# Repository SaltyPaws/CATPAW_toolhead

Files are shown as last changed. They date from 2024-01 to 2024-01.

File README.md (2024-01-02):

# CATPAW_toolhead

CatPaw is the ideal toolhead for Voron Zero series with Orbiter 2.0 Extruder. I developed this toolhead as I was unhappy with the existing options. The standard Voron Zero 0.2 toolhead does not provide as much cooling as I prefer, and certainly less than the StealthBurner toolhead. My design goals were also minimum loss of print volume and maximum compatibility with toolheads and options for probe and filament sensor.

CATPAW:
- Uses Voron Zero 0.2 toolhead cartridges, so should work with all toolheads for voron Zero 0.2 (fan saver recommended)
- 2x 4010 Blowers, with StealthBurner duct layout for near arctic level part cooling (2x 4010 provides more air than StealthBurner toolhead)
- Almost no loss in print volume. X axis should be full width, loss off a millimeter or so on X if you print with your door closed. (Magnets on my door are strong enough, so the door closes again if the toolhead bumps into it, giving me the full 120x120 mm even when printing ABS
- Option to add the slideswipe Probe. I shortened the probe, but all other parts can be used from https://github.com/SaltyPaws/Voron_0.1and0.2mods/SlideSwipe or original repo (https://github.com/chestwood96/SlideSwipe)
- Option to add under extruder filament Sensor
- Carriages are provided for MGN7 and MGN9 X-axis rails. It is recommended to print the provided X carriage for the appropriate rail. In order to minimize toolhead height, I lowered the screw hole for the rear mounting screw.
The CATPAW toolhead will work with the stock Voron Zero 0.2 Carriage, but the screw securing the X-carriage from the rear will not fit.

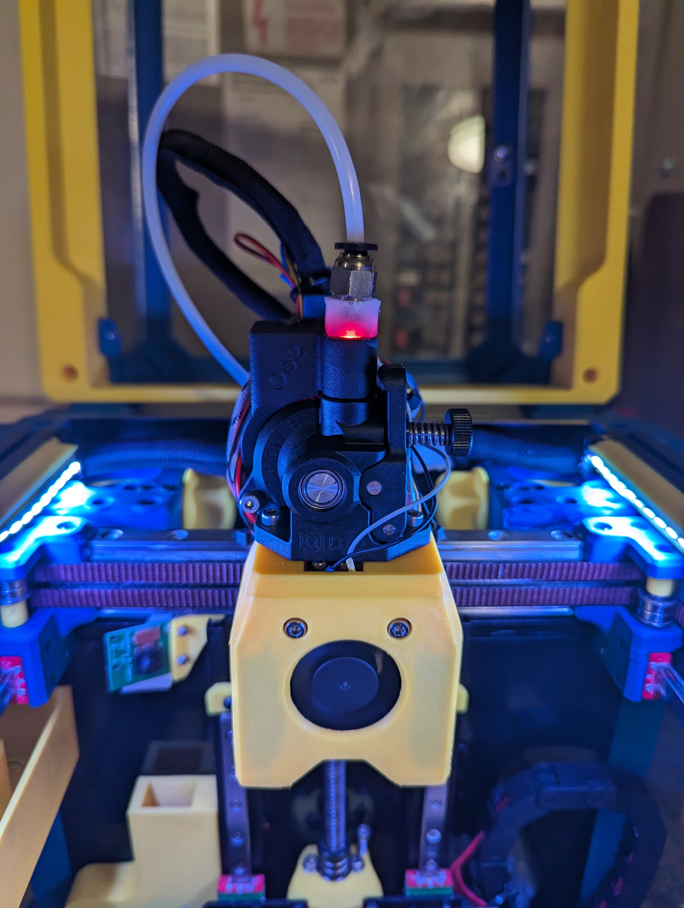
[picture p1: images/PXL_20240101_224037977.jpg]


**BOM**
1. 2x SHCS (preferred) or BHSC M3x25 bolt
2. 3x M3 nut
3. 2x NeoPixel
4. 1x 3010 hotend fan
5. 2x 4010 Blower
6. 6x3mm magnets for probe (optional)
7. 6mm steel ball for filament sensor (optional)
8. Omron D2F-L micro-switch with lever for filament sensor (optional)
9. 2x M2x12 or self-tapping screw to secure micro-switch (optional)

# Installation Instructions
Assembly should be done in the following order:
**Probe**
- Solder wires to 6x3mm magnets. In order to prevent loss of magnetism, let the magnets cool against another 6x3 magnet.
- Press the magnets into the slots by pushing the toolhead down on a hard object.
- Use a large flat soldering tip at around 230C to push the magnets deeper into the slots, you want the magnets to stick out ~0.5 to 1 mm. Again, let the magnets cool down attached to other magnets to prevent loss of magnetism.
- Ensure wire to magnet path has very low resistance (less than 4 ohm).
- route wires out trough little side window.
- Seal hole with red gasket maker.

**NeoPixels**
- Create a chain of 2 neopixels. You do not have a lot of space to hide excess cable, so make the wires between the neopixels as short as possible, while still allowing them to slide into the slots.
- Test the neopixels! It will be more rework to remove the hotend fan and part cooling fans later.

**Fans**
- First install 3010 part cooling fan. Be very careful to only press the edges of the fan, the fan will break when pushing the center of the fan (ask me how I know...)
- Then proceed with installing the blower fans.
- Use a knife to cut the upper right hand side of the blower fan (looking back to front). This is required for routing the majority of the wires. I used superglue to keep the fan together as you will remove a fan closing latch. I accidentally cut int the fan-box, and sealed up the hole with red gasket maker. For details - see pictures below:

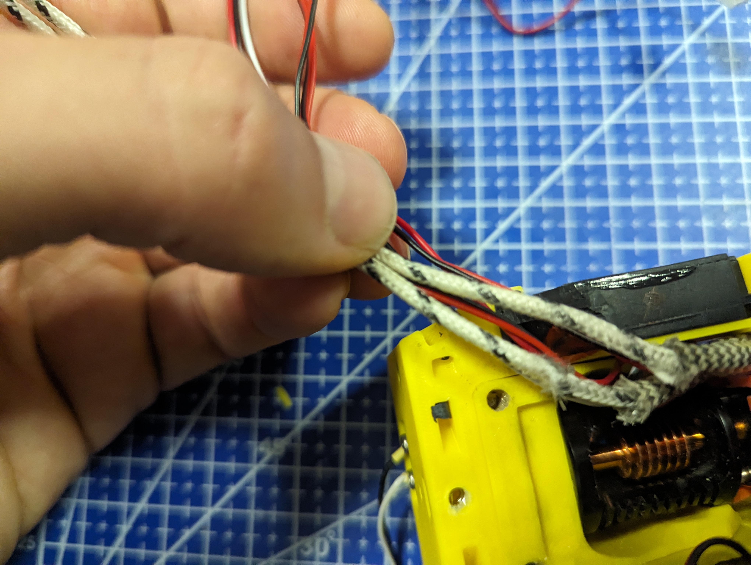
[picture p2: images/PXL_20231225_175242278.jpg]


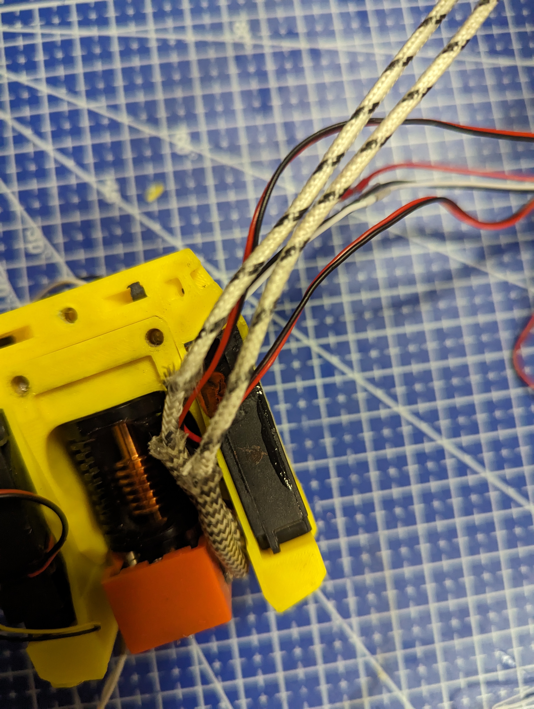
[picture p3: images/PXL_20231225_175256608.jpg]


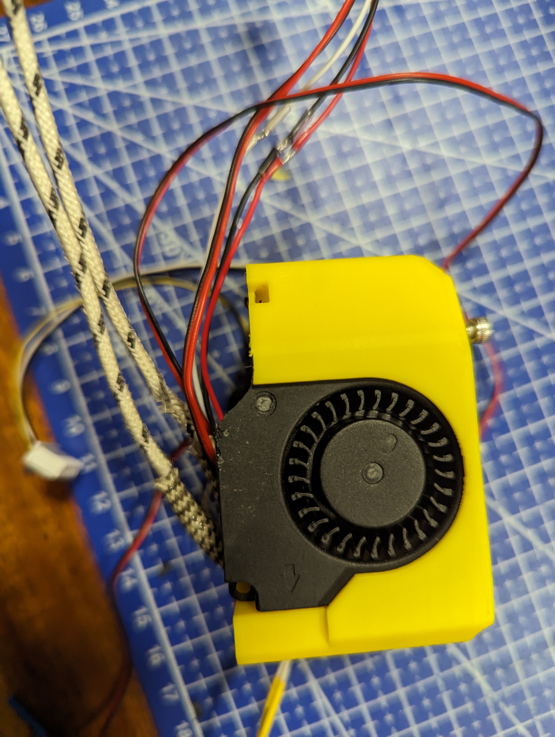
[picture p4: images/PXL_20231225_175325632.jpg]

  
**Toolhead Cartridge**
- Ensure the heater wires are installed pointing towards the right hand fan that has space for wire routing.
- Thermistor, probe and fan wires will fit on the other side (left hand side fan).
- Hold off on installing the zip-ties, these are best installed after the toolhead is installed on the carriage.

**Filament Sensor**  
- Solder wires to filament sensor (2 outermost legs). You may want to shorten the legs somewhat for an easier fit.
- Trim lever, so that lever does not extend past micro-switch body
- Install micro-switch and ball
- Test sensor

**Install Toolhead**
- Carefully mount toolhead, ensuring that wires are not pinched, and belt is not rubbing on gantry. The bulk of the wires will go in the gap carved out on the right hand side fan, the other side will have sufficient space for probe and fan wires.
- 
**Min Probe**
- See installation instructions in orignal repo: https://github.com/chestwood96/SlideSwipe

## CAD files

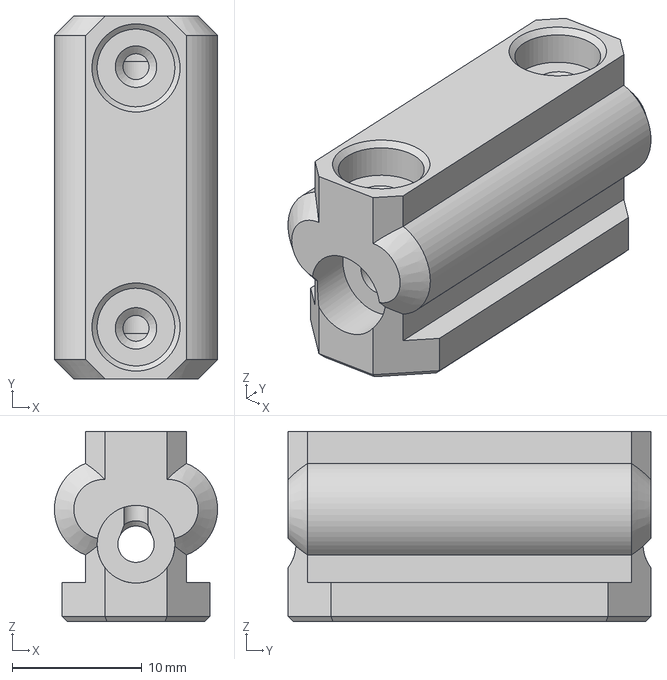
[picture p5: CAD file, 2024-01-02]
CAD/Mini_ProbeTight v3.step
12.6 x 28.0 x 14.7 mm

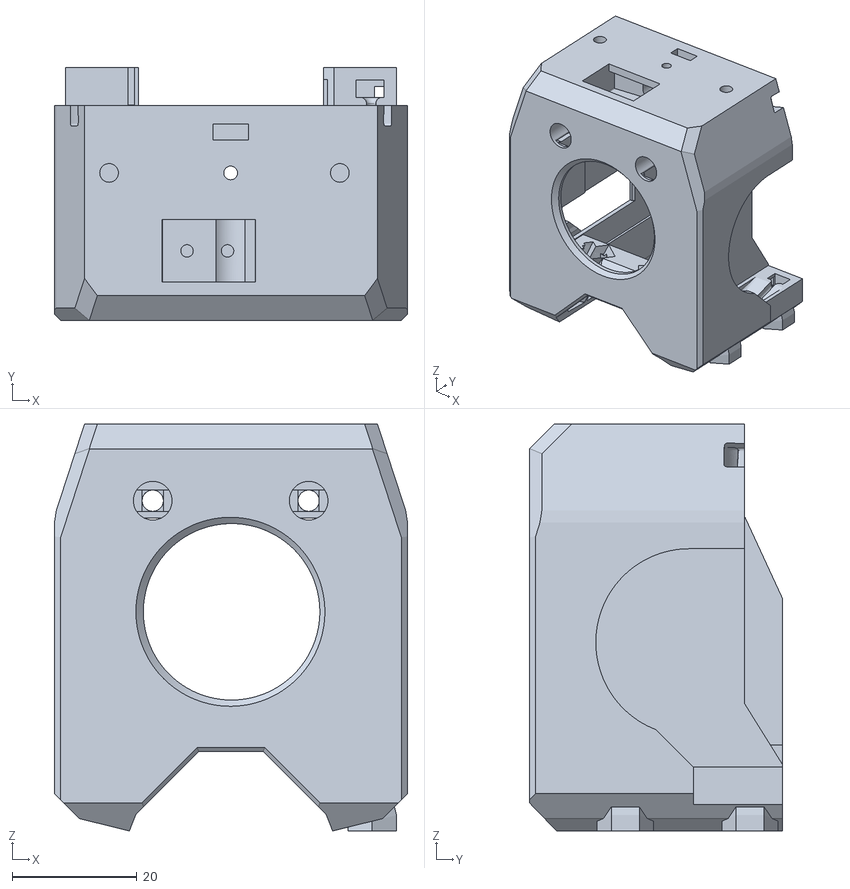
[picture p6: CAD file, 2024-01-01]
STL/Cowling with probe_sensor.stl
56.6 x 40.6 x 65.3

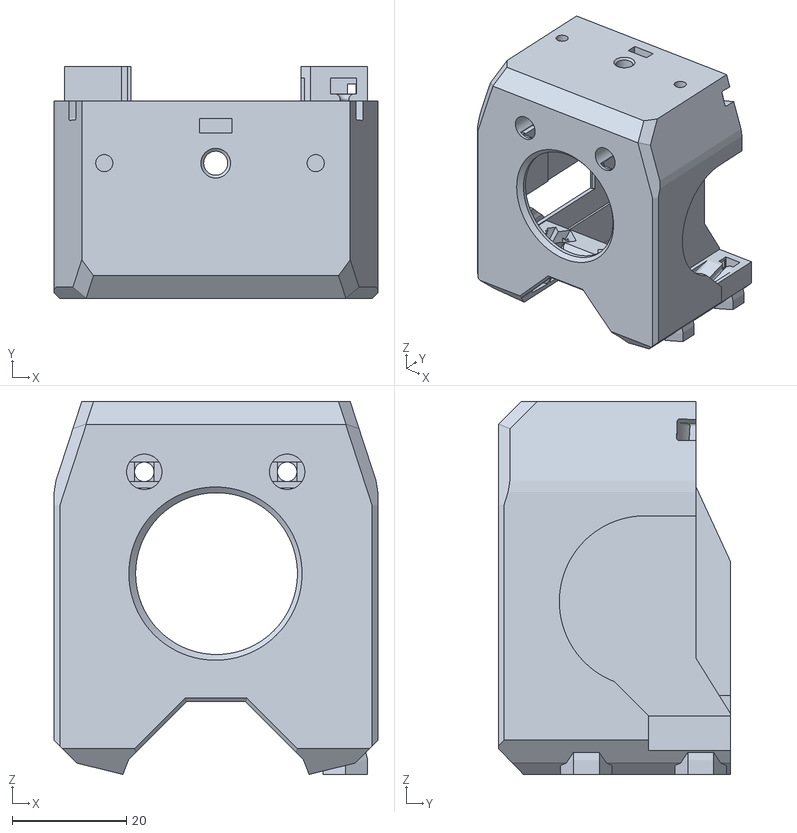
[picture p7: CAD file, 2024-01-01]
STL/Cowling_probe_no_sensor.stl
56.6 x 40.6 x 65.3

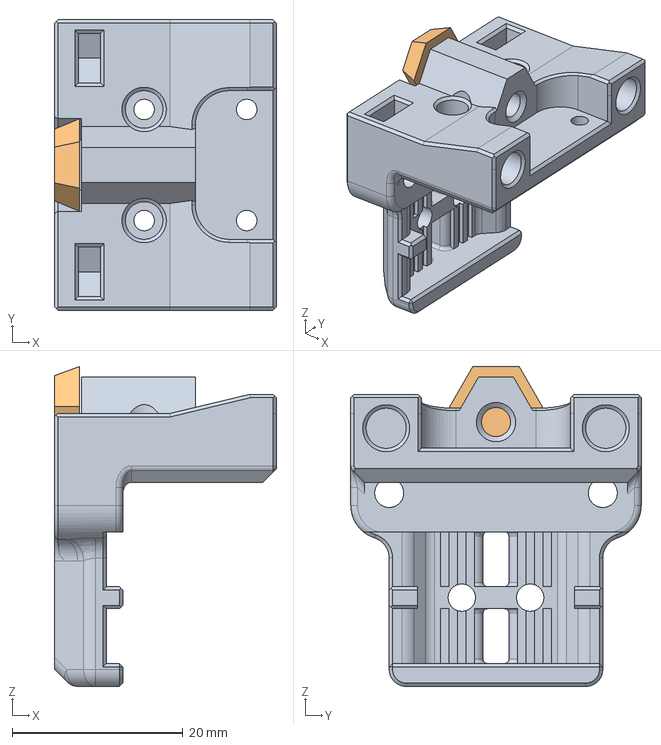
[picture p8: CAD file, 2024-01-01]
CAD/X Carriage_MGN7 v1.step
26.0 x 34.0 x 37.5 mm
X Carriage Body
X Carriage Support

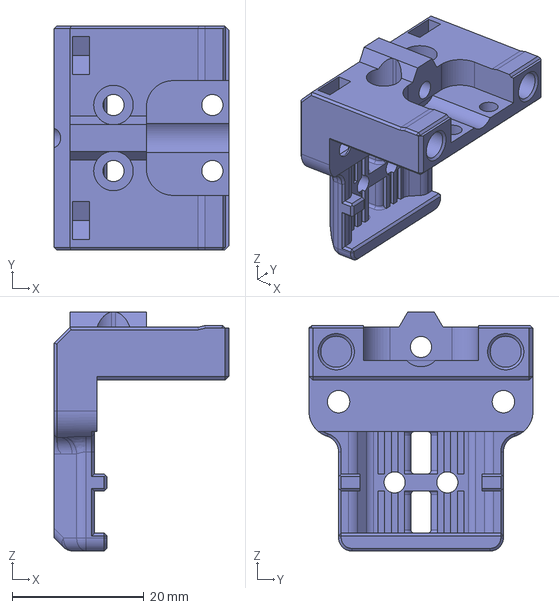
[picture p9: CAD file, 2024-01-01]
CAD/X Carriage MGN9 v1.step
26.5 x 34.0 x 36.2 mm

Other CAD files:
CAD/Mini_ProbeLoose v2.step
STL/Cowling no sensor_no_probe.stl
STL/Cowling sensor_no probe.stl
CAD/Mini_ProbeLoose v2.f3d
CAD/Mini_ProbeTight v3.f3d
STL/Mini_ProbeLoose v2.3mf
STL/Mini_ProbeTight v3.3mf
STL/X Carriage MGN9 v1.stl
STL/X Carriage_MGN7 v1.stl
